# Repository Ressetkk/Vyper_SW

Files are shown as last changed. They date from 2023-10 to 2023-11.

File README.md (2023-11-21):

# Anycubic Vyper to Voron Switchwire Conversion Ver1

This repository contains files and information about conversion of Anycubic's one of the popular and affordable printers, Anycubic Vyper, to Voron Switchwire.
This mod is based on DaRk_dOg's amazing [Ender_SW conversion](https://github.com/boubounokefalos/Ender_SW) and official designs from [Voron's Switchwire repository](https://github.com/VoronDesign/Voron-Switchwire/). The idea of this conversion was generally to provide full CoreXZ motion with Direct Drive and linear rails for Vyper. Additionally enclosing printer in a reasonable way to let print heat resistant plastics with all electonics outside of the printer. Because of the CoreXZ mounting system the build space is around 242x250x255 mm.

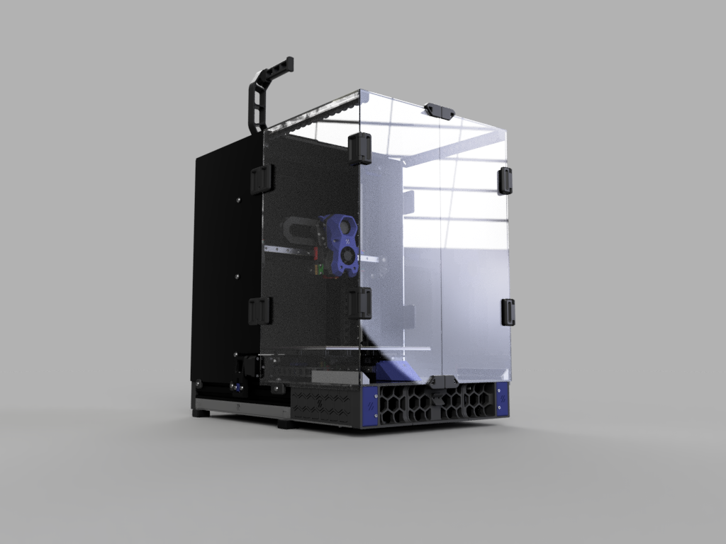
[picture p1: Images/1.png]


## What's been changed

* Y-axis
    * Y-carriage got major overhaul. It is still based on the Ender_SW project, but it was widened to fit 6040 T-shaped extrusion.
    * Y endstop was moved to the carriage. It allows the bed to park on the front, just like in original Switchwire.
    * Added ADXL mounts to the left carriage inspired by Stealthburner mounts. Different sensor hole sizes are available. Spacers from original Stealthburner ADXL mounts are required to install sensor on the mount.
    * Y-carriage is compatible with stock bed assembly including it's 12 screws mounts. There is enough clearance for the screws to not interfere with the assembly.
    * Y-idler has been widened to cover entire 6040 T-shaped extrusion and includes a small notch that helps triggering the Y-endstop on the carriage.
    * Designed small Y-axis stoppers that fit both 300 mm and 350 mm rails mounted on Y-axis.
    * Added Y-axis motor mount that extends the Y-axis to properly mount the motor on rear grill (based on Ender_SW EV2 variant). it also covers extrusion holes.
* XZ-Axis
    * Adjusted XZ-blocks to fit 300 mm linear rail on 330mm X-axis assembly. It follows original Switchwire design and uses 2x M5x16 screws to mount to the front of extrusion.
    * Created aditional variant of XZ-blocks to fit 2020 T-slot extrusion (if you bought one, like me).
    * Created new and bigger Z-axis stoppers that use M5x10 to mount to the frame to match Keybak mount sizes.
    * Keybak mount got adjusted and resized to fit 4020 side extrusion and serves as Z stop.
* Frame extensions
    * Rear extensions got resized to match Vyper's size.
    * Front extensions now allow mounting 2x 6020 fans on the front of the printer with small mount that uses 2 threaded inserts and 2x M3x8 screws. To mount 6020 fan you need 2x M3x25 screws.
* Grills
    * Front- and Rear- middle grills got adjusted to match the size of a Vyper.
    * Added rear left grill for stock power outlet from Fizzytech's take on their, also amazing, "[FT Vyperwire](https://github.com/fizzystech/vyperwire)" project.
    * 
* Electronics
    * Added Anycubic TriGorilla v0.0.6+ frame mount.
    * Created small PSU mounts that allow to mount PSU on either front, or back of the frame, depending on preference.
* Panels
    * Resized all panels to match Vyper's size.
    * Light bars got resized to match Vyper's size.
* Misc
    * Added hole cover for frame cross-section the 54mm one is for C revision and onwards printers, whereas smaller one is for A and B revision ones.

## What can be salvaged

Here are the parts that can be salvaged for building the conversion:
* Frame, excluding top and X-axis extrusion (you have to replace them)
* Possibly stepper motors, but they may not have enough torque, so YMMV
* Entire bed assembly
* Mainboard - you can "enable" UART mode with some soldering work without any problems
* Extruder - Yes! It's a BMG clone, so the gears should be fitting to Clockwork 2. Unfortunately I had some problems with the size of the bearings, so YMMV
* PSU - It's a knock-off MeanWell LRS-350-24
* Heatbreak 4010 fan
* Screws, bolts and PTFE tube

## BOM Changes

The BOM is the same for Official Switchwire with Ender_SW changes. Also include the things below.

|Name|Qty|Note|
|---|---|---|
|M3x16 BHCS (ISO 7380-2)|2|XZ-blocks mount|
|M3x8 SHCS (DIN 912)|at least 6|ADXL and front fan mounts|
|M3x25 SHCS (DIN 912)|4|Optional. front fan mounts|
|M2x10 self-tapping screws|2|ADXL mount|
|M5x10 BHCS (ISO 7380-2)|at least 4|Z rail stops mounts|
|M3x5x4 threaded inserts|at least 6|ADXL mount and front fans mount. The same inserts as in Voron specs|
|300 mm MGN12H rails|3|X and Y axes. You can use 2x 350 mm for Y axis if you have them, otherwise buy cheaper option|
|350 mm MGN12H rails|2|Z axis. See note above|
|330 mm 2020 V-slot extrusion|1| X-axis replacement. If you can, buy 2 350 mm extrusions and cut one to the size with a saw|
|350 mm 2020 V-slot extrusion|1| Top frame. See note above|
|6020 GDSTIME or Sunon Fans|2|Optional. For front fan mounts|

## Printing options

Follow official VoronDesign guides and suggestions on how to print your parts. For the toolhead STLs, use official [Voron Stealthburner]() release. 

## Credits
* [Voron Design](https://vorondesign.com/) - for official Voron Switchwire project and STLs
* DaRk_dOg (aka [boubounokefalos](https://github.com/boubounokefalos)) - for amazing [Ender_SW conversion](https://github.com/boubounokefalos/Ender_SW)
* [Fizzytech](https://github.com/fizzystech) and their Discord - for some ideas and files taken from their modded conversion
* You - for reaching out this far :) Thanks!

# License

The files are distributed under GNU GPL v3.0 license.

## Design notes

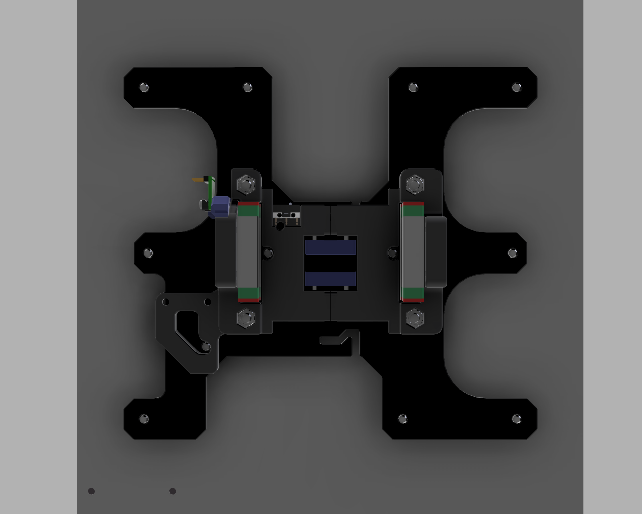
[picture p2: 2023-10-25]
Images/carriage.png

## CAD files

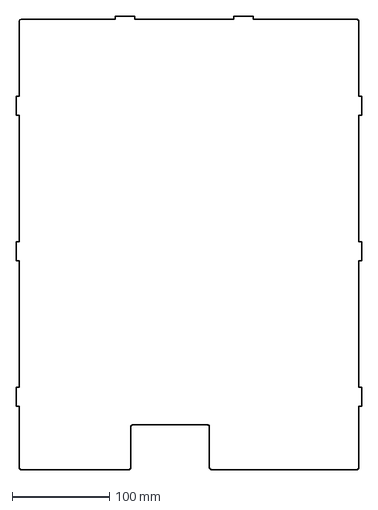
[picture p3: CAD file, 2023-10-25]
DXF/rear_back.dxf
356.0 x 467.0 mm

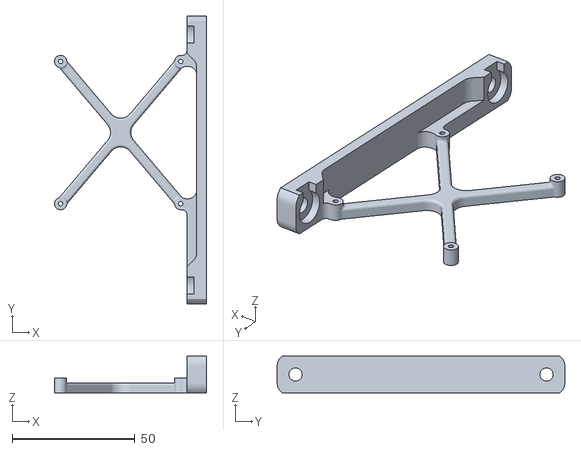
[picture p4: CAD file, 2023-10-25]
STL/Electronics/rpi_mount.stl
62.0 x 117.4 x 15.0

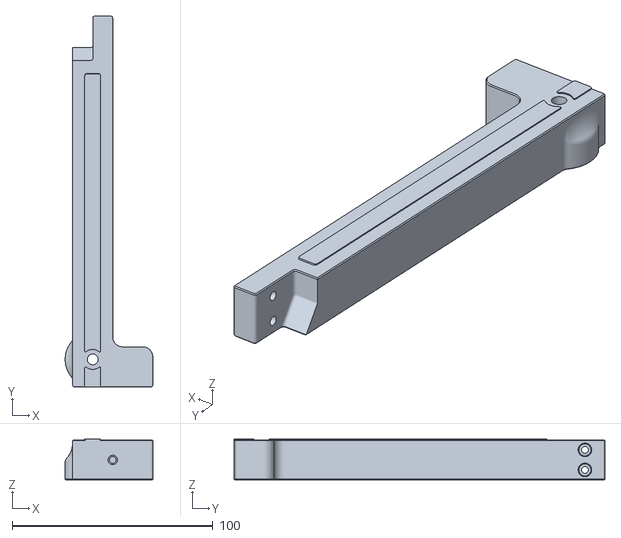
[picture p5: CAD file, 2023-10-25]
STL/Extensions/rear_extension_left_a.stl
43.8 x 184.9 x 20.4

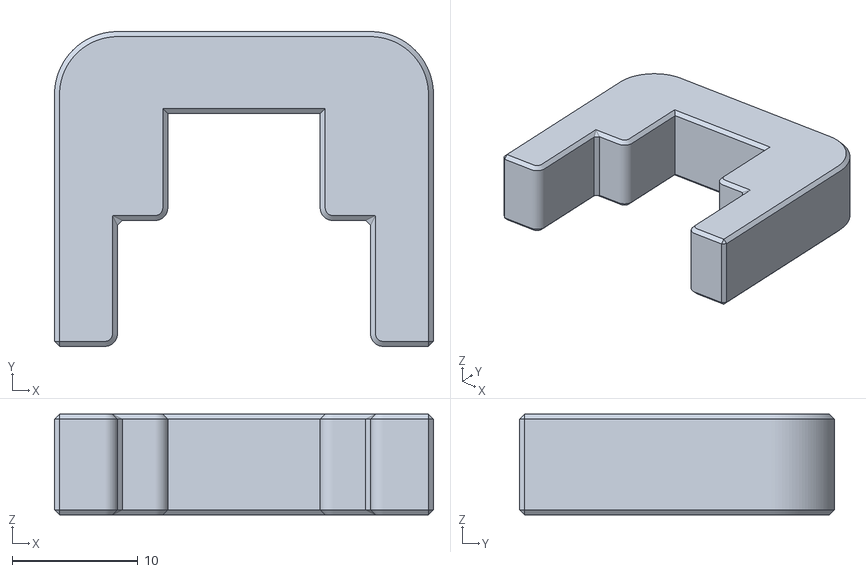
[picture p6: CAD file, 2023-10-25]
STL/Gantry/2020_MGN12_guide_x2.stl
30.1 x 25.0 x 8.00

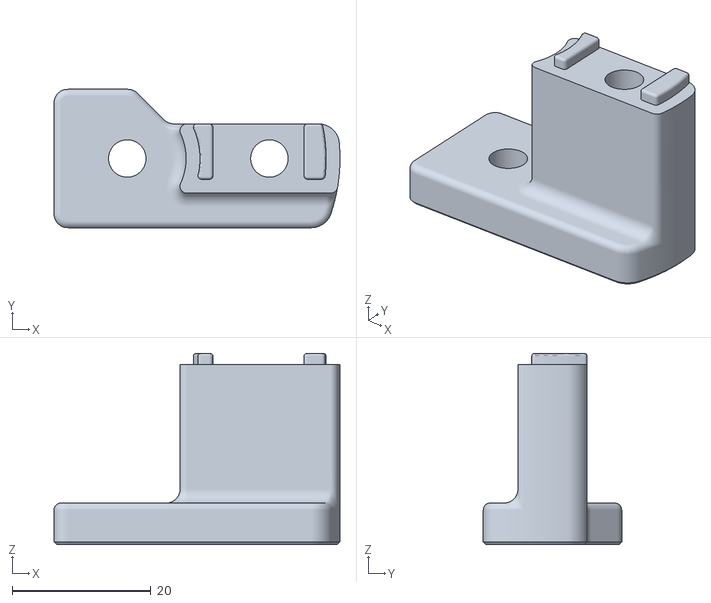
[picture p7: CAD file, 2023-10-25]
STL/Gantry/XZ Axis/upper_idler_support_a_left.stl
41.3 x 20.0 x 27.6

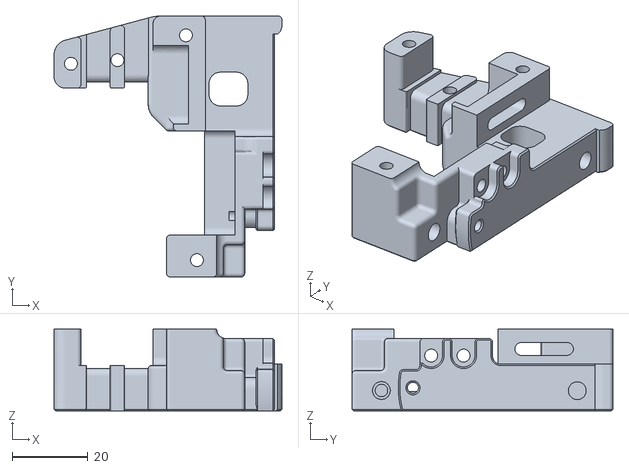
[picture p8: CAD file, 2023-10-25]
STL/Gantry/XZ Axis/X_Carriage/x_frame_SW_left.stl
60.0 x 68.8 x 21.6

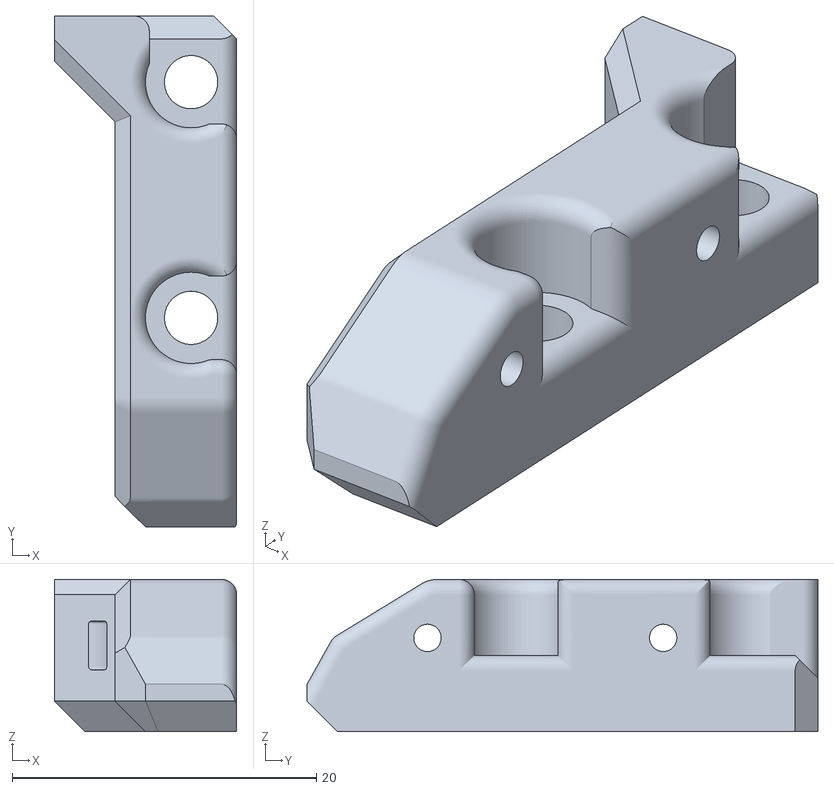
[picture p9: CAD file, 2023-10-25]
STL/Gantry/Y Axis/ADXL mounts/adxl_mount_generic_15_5cm.stl
12.0 x 33.6 x 10.00

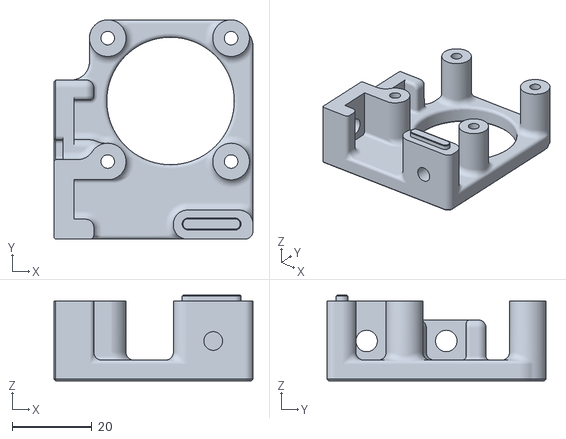
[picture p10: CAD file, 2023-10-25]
STL/Gantry/Y Axis/y_motor_mount_a.stl
50.0 x 55.1 x 21.5

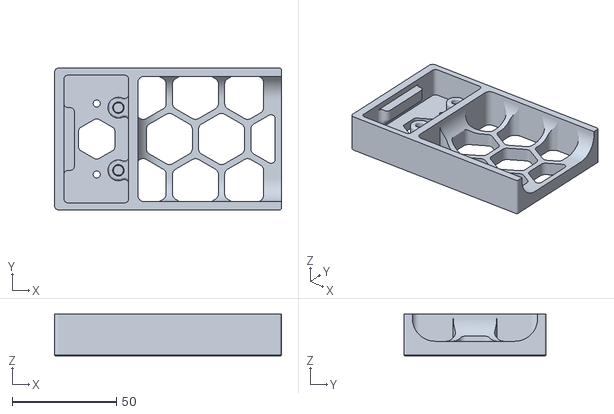
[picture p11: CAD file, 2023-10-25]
STL/Grills/grill_front_right.stl
108.7 x 68.0 x 20.0

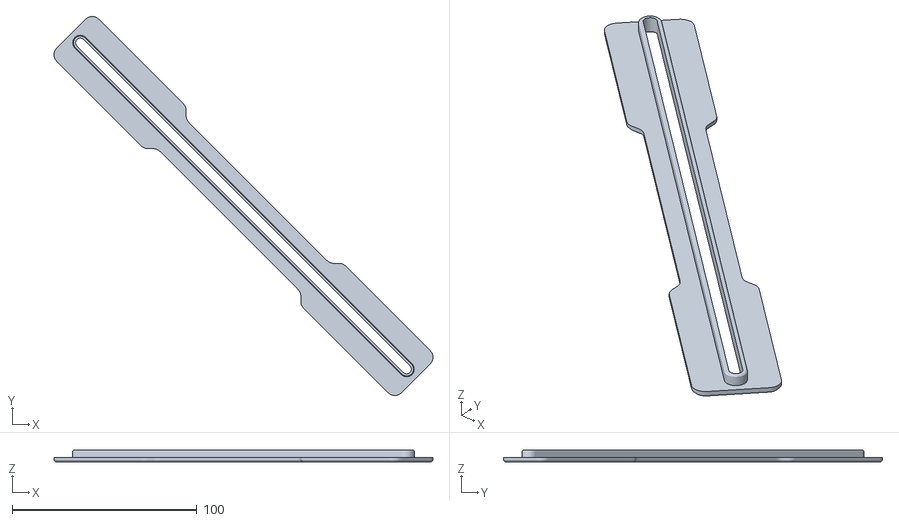
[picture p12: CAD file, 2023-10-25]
STL/Panels/feed_slot.stl
205.3 x 205.3 x 6.40

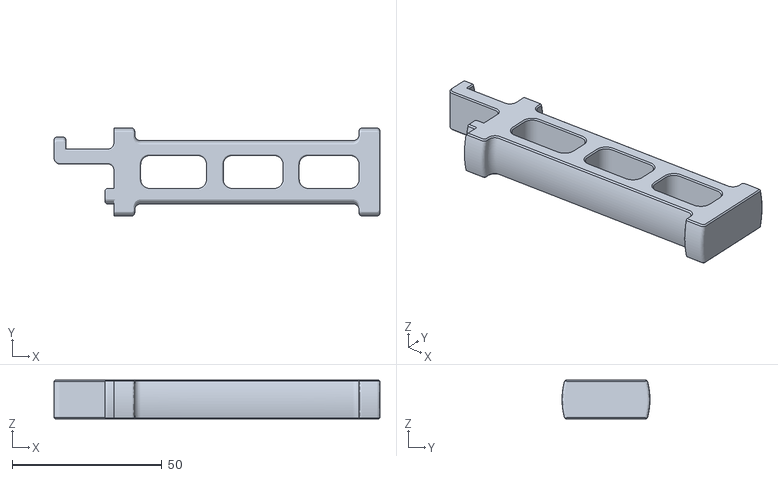
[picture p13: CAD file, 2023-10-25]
STL/spool_holder.stl
109.0 x 29.4 x 13.0

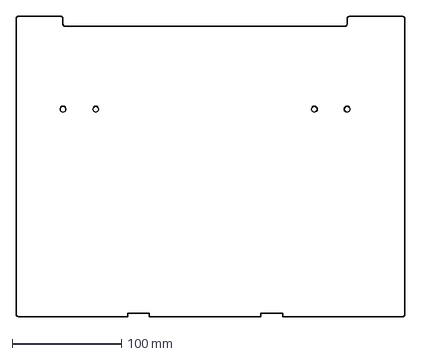
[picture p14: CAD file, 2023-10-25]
DXF/rear_top.dxf
356.0 x 275.0 mm

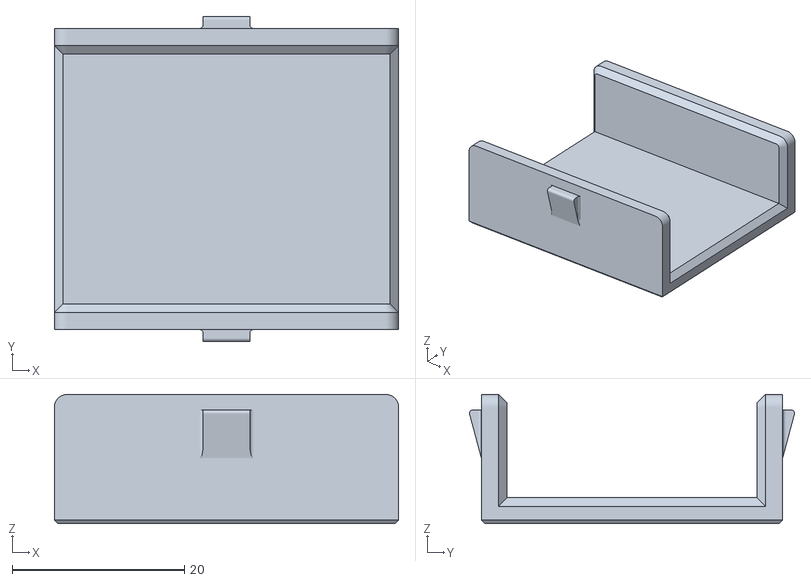
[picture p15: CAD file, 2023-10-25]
STL/cross_section_hole_cover_B.stl
40.0 x 37.8 x 15.0

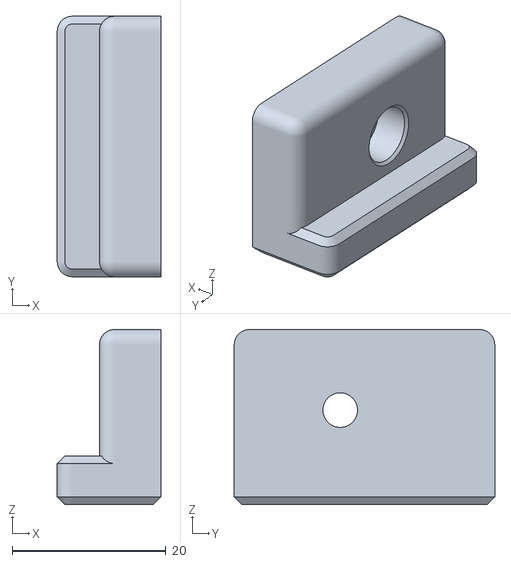
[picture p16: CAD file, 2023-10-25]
STL/Electronics/psu_mount_b.stl
13.5 x 33.9 x 22.8

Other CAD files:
STL/Extensions/front_extension_right_b.stl
STL/Gantry/XZ Axis/X_Carriage/[a]_xz_belt_clip_x2.stl
STL/Gantry/XZ Axis/xz_block_right_a_t_slot.stl
STL/Gantry/Y Axis/[a]_y_chain_bed_mount_igus.stl
DXF/bottom.dxf
DXF/deck_x2.dxf
DXF/rear_side_x2.dxf
STL/2mm_spacer.stl
STL/Electronics/anycubic_trigorilla_mount.stl
STL/Electronics/psu_mount_a_front_x2.stl
STL/Electronics/psu_mount_a_side.stl
STL/Extensions/Front Extention A.stl
STL/Extensions/fan_mount_x2.stl
STL/Extensions/front_extension_left_a.stl
STL/Extensions/front_extension_left_b.stl
STL/Extensions/front_extension_support_arm_x2.stl
STL/Extensions/rear_extension_left_b.stl
STL/Extensions/rear_extension_right_a.stl
STL/Extensions/rear_extension_right_b.stl
STL/Gantry/XZ Axis/X_Carriage/[a]_x_bearing_block.stl
STL/Gantry/XZ Axis/X_Carriage/probe_retainer_bracket.stl
STL/Gantry/XZ Axis/X_Carriage/x_frame_SW_right.stl
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

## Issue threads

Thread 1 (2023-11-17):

2x 350mm Frame

Fragmon, 2023-11-17:
Thank you for this repo. Is this a TYPO? You write 2x 350mm and 1x330. I think you mean 1x 350 and 1x 330mm or 2x350 and cut one down?

Ressetkk, 2023-11-21:
Exactly!
2x 350mm 2020 extrusions and cut one down to 330mm, or 1x 350 mm and 1x 330mm to avoid cutting.

Ressetkk, 2023-11-21:
Fixed incorrect count of 350mm extrusions.

Closed 2023-11-21.

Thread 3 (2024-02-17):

Printer.cfg

Eliasklassen, 2024-02-17:
Hey there and thank you so much for dis conversation. It works pretty good und im almost done. I did the tmc uart upgrade with my og mainboard but I can’t find information were the uart pins are after the wiring. If you printing with Klipper, I would be very happy to see/copy your printer.cfg.
Ty

Ressetkk, 2024-03-12:
I have avoided it because Klipper configuration may vary depending on the user configuration. However I can think of providing some basic configurations.
